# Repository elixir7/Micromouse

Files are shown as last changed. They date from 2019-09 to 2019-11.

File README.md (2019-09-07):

# Jerry the micromouse
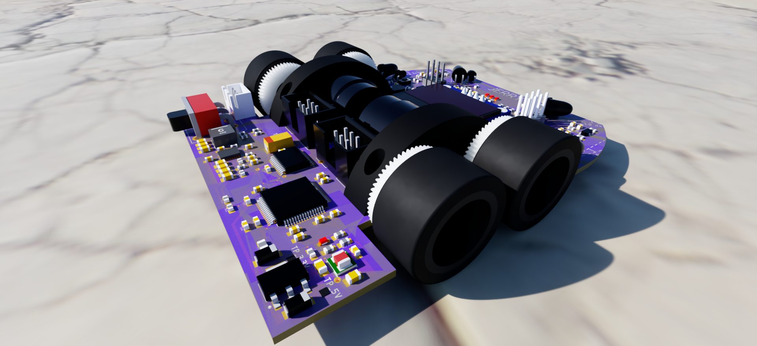
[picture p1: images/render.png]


# Who is Jerry?
Jerry is a tiny (10x8 cm) high performance robot for the robotics competition Micromouse. 

The competition goal is to search a 16x16 grid maze which is 3x3 m^2 as fast as possible and find the path to the center.

Then you run from start to goal with your calculated route. 

To get the competition you take 1/30 of the search time and the run time.

World class mice are extremly fast, [have a look.](https://www.youtube.com/watch?v=NqdZ9wbXt8k&t=150s)

# Structure & Development
Hardware:
-   <b>3D_Models</b>,       pcb components, motor mount, rims etc.
-   <b>drawings</b>,        .dxf files
-   <b>pcb</b>,             EAGLE CAD files
-   <b>gerbers.zip</b>,     manufacturing files for pcb (Jerry was made by [JLC PCB](https://www.jlcpcb.com)
-   <b>jlcpcb.cam</b>,      CAM job for creating gerber files to JLC standard in EAGLE.

Software:
-   <b>Eagle</b>,           E-CAD for making PCB
-   <b>Fusion 360</b>,      M-CAD for making board outline, motor mounts, rims, etc.
-   <b>Keil uVision 5</b>,  IDE for C programming/debugging on Microcontrollers

Images:
-   Renders of jerry

## Software
- MCU configuration (pins, clock, etc) using STM32CubeMX
- Keil uVision 5 project
    - Low level drivers (motors, sensors, screen)
    - High level maze solving algoritm

## Contributors
-   Isak Åslund, aslundisak@gmail.com

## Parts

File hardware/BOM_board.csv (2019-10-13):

Cart | # | Placed | Parts | Value | Package | Qty | Description | Device | TOLERANCE | V_RATING | Vendor | Link
x | 1 |  | BOOT |  | 2X03 | 1 | PIN HEADER | PINHD-2X3 |  |  | case/crf
x | 2 |  | DEBUG |  | 2X04 | 1 | PIN HEADER | PINHD-2X4 |  |  | case/crf
x | 3 |  | R32, R35, R36, R37 | 0 | R0603 | 4 | Standard Chip RESISTOR 0603 (1608 Metric) | R0603 |  |  | mouser
x | 4 |  | C1, C2, C4, C6, C8, C10, C12, C14, C18, C28, C30, C34, C35, C36, C43, C47, C48, C49, C50, C51 | 0.1u | C0603 | 20 | Standard Chip CAPACITOR 0605 (1608 Metric) | C0603 |  |  | mouser
x | 5 |  | C16 | 0.1u | C0805 | 1 | Standard Chip CAPACITOR 0805 (2012 Metric) | C0805 |  |  | mouser
x | 6 |  | R6, R7, R9, R12 | 0.75 | R0603 | 4 | Standard Chip RESISTOR 0603 (1608 Metric) | R0603 |  |  | mouser
x | 7 |  | R1, R2, R13, R16 | 1.8k | R0603 | 4 | Standard Chip RESISTOR 0603 (1608 Metric) | R0603 |  |  | mouser
x | 8 |  | R29 | 100k | R0603 | 1 | Standard Chip RESISTOR 0603 (1608 Metric) | R0603 |  |  | mouser
x | 9 |  | R_FBT | 105k | R0603 | 1 | Standard Chip RESISTOR 0603 (1608 Metric) | R0603 |  |  | mouser
x | 10 |  | R23 | 10k | R0603 | 1 | Standard Chip RESISTOR 0603 (1608 Metric) | R0603 | 1% |  | mouser
x | 11 |  | R3, R8, R10, R11, R15, R24, R27, R30, R31, R33, R34 | 10k | R0603 | 11 | Standard Chip RESISTOR 0603 (1608 Metric) | R0603 |  |  | mouser
x | 12 |  | C5, C7, C9, C11, C13, C42 | 10u | C0603 | 6 | Standard Chip CAPACITOR 0605 (1608 Metric) | C0603 |  |  | mouser
x | 13 |  | C_IN, C_OUT | 10u | C0805 | 2 | Standard Chip CAPACITOR 0805 (2012 Metric) | C0805 |  |  | mouser
x | 14 |  | C3 | 10u | EIA_6032-28 | 1 | KEMET C Size Taltalum Capacitator | KEMET_C |  |  | mouser
x | 15 |  | C26, C27 | 10u | SMC_A | 2 | A Size Taltalum Capacitator | SMC_A |  |  | mouser
x | 16 |  | FP1, FP2 | 10u | R0805 | 2 | Würth Electronics Size 0805 Ferrite Pearls | WE-CBF_0805 |  |  | mouser
x | 17 |  | R21 | 112k | R0603 | 1 | Standard Chip RESISTOR 0603 (1608 Metric) | R0603 |  |  | mouser
x | 18 |  | R17, RB | 150k | R0603 | 2 | Standard Chip RESISTOR 0603 (1608 Metric) | R0603 |  |  | mouser
x | 19 |  | R18 | 180k | R0603 | 1 | Standard Chip RESISTOR 0603 (1608 Metric) | R0603 |  |  | mouser
x | 20 |  | U$1 | 1N4148WX | 1N4148WX_SOD-323-2 | 1 |  | DIODE_1N4148WX |  |  | mouser
x | 21 |  | R4, R5, R14, R25 | 1k | R0603 | 4 | Standard Chip RESISTOR 0603 (1608 Metric) | R0603 |  |  | mouser
x | 22 |  | C44 | 1u | C0603 | 1 | Standard Chip CAPACITOR 0605 (1608 Metric) | C0603 |  |  | mouser
x | 23 |  | C24 | 1u | C0805 | 1 | Standard Chip CAPACITOR 0805 (2012 Metric) | C0805 |  |  | mouser
x | 24 |  | C15, C29, C45, C46 | 2.2u | C0603 | 4 | Standard Chip CAPACITOR 0605 (1608 Metric) | C0603 |  |  | mouser
x | 25 |  | L1 | 2.2u | XAL5030 | 1 | COILCRAFT - XAL5030-222MEC - INDUCTOR, PWR, 2.2UH, 9.2A,20%,38MHZ | XAL5030-222MEC |  |  | mouser
x | 26 |  | R19, R26, R28, R_FBB | 20k | R0603 | 4 | Standard Chip RESISTOR 0603 (1608 Metric) | R0603 |  |  | mouser
x | 27 |  | C17, C19, C20, C22, C25 | 22u | C0805 | 5 | Standard Chip CAPACITOR 0805 (2012 Metric) | C0805 |  |  | mouser
x | 28 |  | C33 | 22u | C0805 | 1 | Standard Chip CAPACITOR 0805 (2012 Metric) | C0805 |  | 10v | mouser
x | 29 |  | C32 | 22u | C0805 | 1 | Standard Chip CAPACITOR 0805 (2012 Metric) | C0805 |  | 25V | mouser
x | 30 |  | C21 | 27p | C0603 | 1 | Standard Chip CAPACITOR 0605 (1608 Metric) | C0603 |  |  | mouser
x | 31 |  | RT | 290k | R0603 | 1 | Standard Chip RESISTOR 0603 (1608 Metric) | R0603 | 1% |  | mouser
x | 32 |  | R20 | 30k | R0603 | 1 | Standard Chip RESISTOR 0603 (1608 Metric) | R0603 |  |  | mouser
x | 33 |  | C31 | 3300p | C0603 | 1 | Standard Chip CAPACITOR 0605 (1608 Metric) | C0603 |  | 10V | mouser
x | 34 |  | C_VC | 470pF | C0603 | 1 | Standard Chip CAPACITOR 0605 (1608 Metric) | C0603 |  | 6.3V | mouser
x | 35 |  | R22 | 47k | R0603 | 1 | Standard Chip RESISTOR 0603 (1608 Metric) | R0603 |  |  | mouser
x | 36 |  | C23 | 560p | C0603 | 1 | Standard Chip CAPACITOR 0605 (1608 Metric) | C0603 |  |  | mouser
x | 37 |  | U4 | BMI088 | PQFN50P450X300X100-16N | 1 | High-performance 6-axis inertial sensor (accelerometer + gyroscope) | BMI088 |  |  | mouser
x | 38 |  | 5V_PWR, LED_B, LED_G, LED_R | CHIP-LED0603 | CHIP-LED0603 | 4 | CHIP-LED0603 (SMD) | CHIP-LED0603 |  |  | mouser
x | 39 |  | OLED | DISPLAY-OLED-128X64-I2C | DISPLAY-OLED-128X64-I2C | 1 | 128x64 Dot Matrix OLED Module based on SSD1306 chip | DISPLAY-OLED-128X64-I2C |  |  | mouser
x | 40 |  | MOTOR_LEFT, MOTOR_RIGHT | IE2-1024-ENCODER | IE2-1024-ENCODER | 2 |  | IE2-1024-ENCODER |  |  | mouser
x | 41 |  | Q1, Q2, Q3, Q4, Q5 | IRFML8244TRPBF | SOT95P235X110-3 | 5 | IRFML8244TRPbF - N Channel Mosfet | IRFML8244TRPBF |  |  | mouser
x | 42 |  | U$10 | JST-XH-3 | JST-XH-03 | 1 |  | JST-XH-3 |  |  | mouser
x | 43 |  | BTN_RST, BTN_SEL | KMR621NGLFS | KMR621NGLFS | 2 | C&K KMR621NG LFS Tactile SPST switch (SMD) | KMR621NGLFS |  |  | mouser
x | 44 |  | VR1 | LM1117-3.3 | SOT230P700X180-4 | 1 | LM1117 | LM1117-3.3 |  |  | mouser
x | 45 |  | IC3 | LMZ10501 | SON65P260X300X150-9N | 1 | Voltage Regulators - Switching Regulators 1A Nano Mod w/ 5.5V Max Inpt VTG | LMZ10501 |  |  | mouser
x | 46 |  | S1 | LMZ21701 | LMZ21701 | 1 | 3V to 17V, 1A Step-Down DC/DC Power Module in 3.5mm 3.5mm Package | LMZ21701 |  |  | mouser
x | 47 |  | FL_EMITTER, FR_EMITTER, L_EMITTER, R_EMITTER | SFH_4545 | SFH_4545 | 4 | High Power Infrared Emitter (940 nm) | SFH_4545 |  |  | mouser
x | 48 |  | U$4 | SMT-0540-S-R | SMT-0540-S-R | 1 | Magnetic buzzer | SMT-0540-S-R |  |  | mouser
x | 49 |  | SW | SPDT-500SSP1S1M6QEA | 500SSP1S1M6QEA | 1 |  | SPDT-500SSP1S1M6QEA |  |  | mouser
NA | 50 |  | U$6, U$7 | SPLITTER | SPLITTER | 2 | Used for separating grounds | SPLITTER |  |  | NA
x | 51 |  | U3 | STM32F405RG | LQFP-64 | 1 | STM32F405RG Microcontroller | STM32F405RG |  |  | mouser
x | 52 |  | U1 | TB6612FNG | SOP65P760X160-24 | 1 | TB6612FNG - Dual DC motor driver | TB6612FNG |  |  | mouser
x | 53 |  | D4, D5, D6, D8 | TEFT4300 | 3MM_PHOTOTRANSISTOR | 4 | TEFT4300 Phototransistor from Vishay | TEFT4300 |  |  | mouser
NA | 54 |  | TP_2V, TP_3.3V, TP_5V, TP_12V | TEST-POINT3X5 | PAD.03X.05 | 4 | SparkFun Test Points | TEST-POINT3X5 |  |  | NA
x | 55 |  | IC2 | TPS61088RHLR | RHL(R-PVQFN-N20)_1 | 1 | DC-DC Boost Regulator | TPS61088RHLR |  |  | mouser
x | 56 |  | HC-05 | WIRELESS-BLUETOOTH-HC-05 | WIRELESS-BLUETOOTH-HC-05 | 1 | Bluetooth Transceiver Module based on HC-05 board | WIRELESS-BLUETOOTH-HC-05 |  |  | mouser

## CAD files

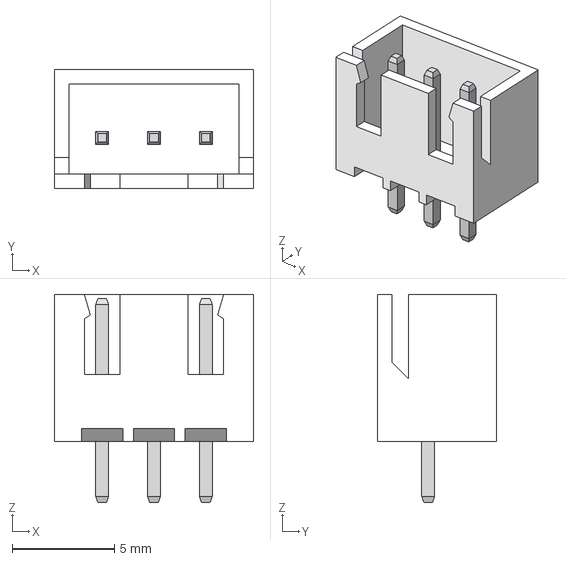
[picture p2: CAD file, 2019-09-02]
hardware/3D_Models/JST-XH-03.step
9.75 x 5.84 x 10.2 mm

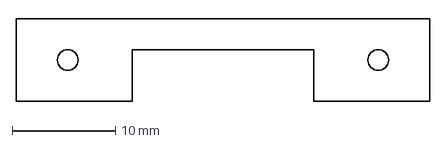
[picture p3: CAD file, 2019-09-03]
hardware/drawings_dxf/motor_mount.dxf
40.0 x 8.00 mm

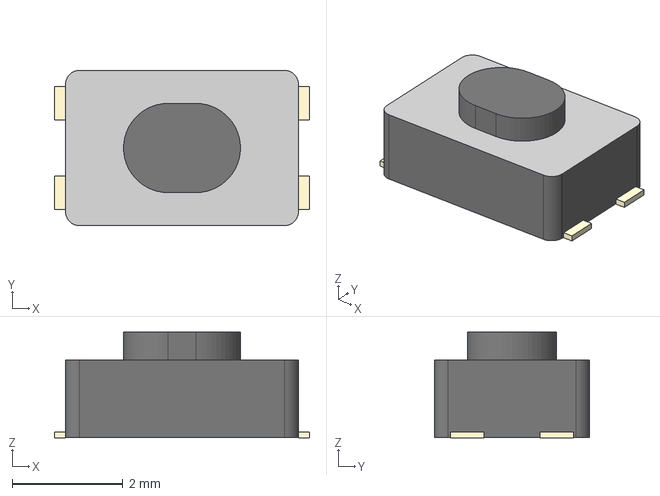
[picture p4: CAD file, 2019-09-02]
hardware/3D_Models/KMR621NGLFS.step
4.60 x 2.80 x 1.91 mm

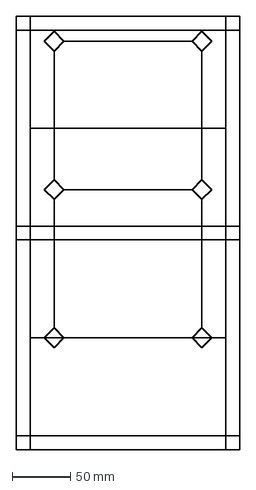
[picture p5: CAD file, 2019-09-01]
hardware/drawings_dxf/maze_dimenions.dxf
192.0 x 372.0 mm

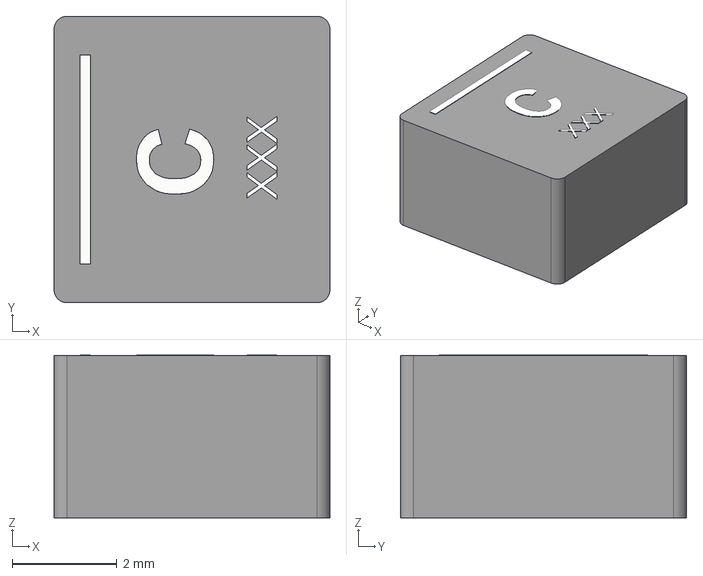
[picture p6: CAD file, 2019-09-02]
hardware/3D_Models/HALX5030-222.step
5.28 x 5.48 x 3.11 mm

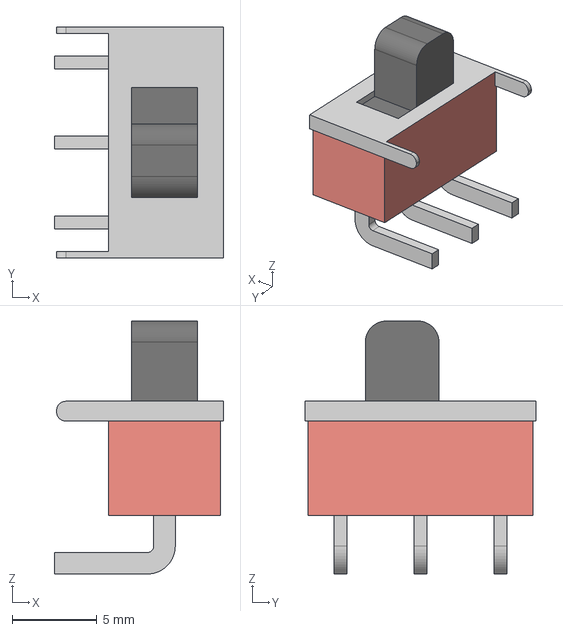
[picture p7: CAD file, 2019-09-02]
hardware/3D_Models/500SSP1S1M6QEA-Switch.step
9.96 x 13.6 x 14.9 mm

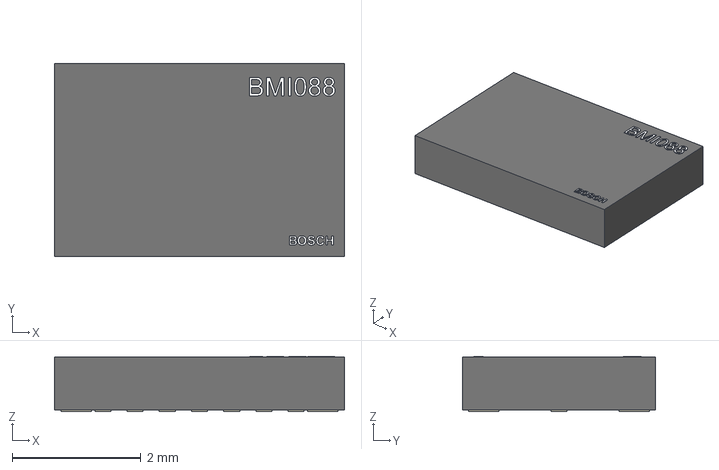
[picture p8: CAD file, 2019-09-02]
hardware/3D_Models/BMI088.step
4.50 x 3.00 x 0.86 mm

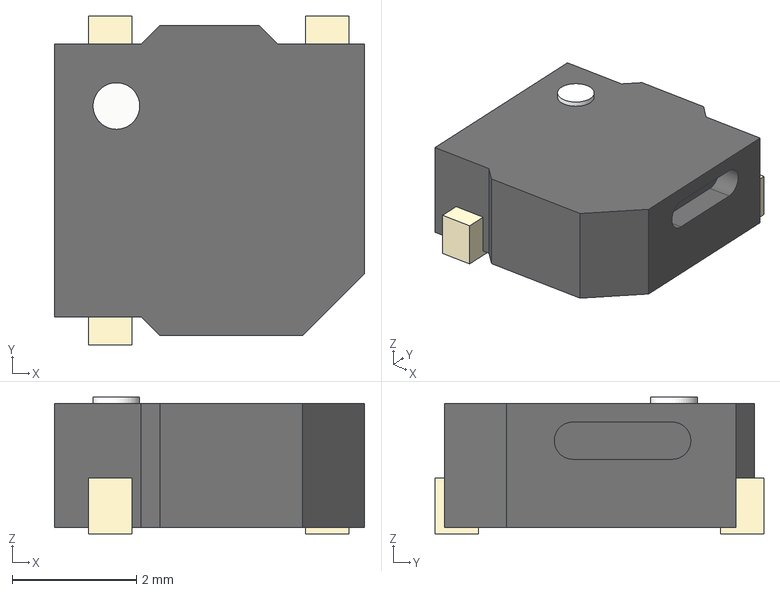
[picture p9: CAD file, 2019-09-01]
hardware/3D_Models/SMT-0540-SR.step
5.00 x 5.30 x 2.20 mm

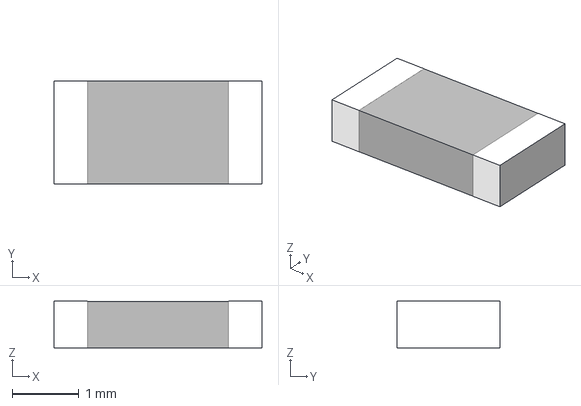
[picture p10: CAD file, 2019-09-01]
hardware/3D_Models/R1206.step
3.12 x 1.55 x 0.7 mm

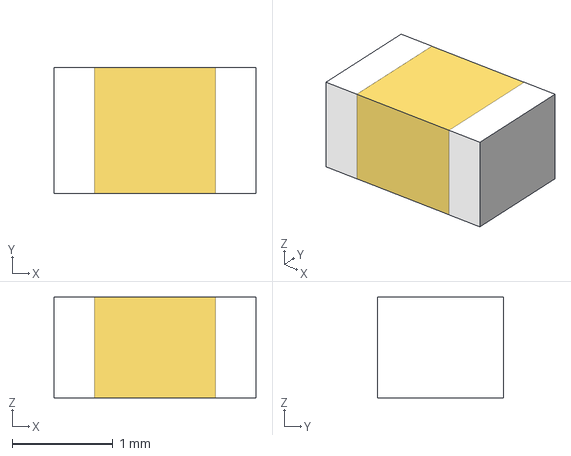
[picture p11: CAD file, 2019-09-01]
hardware/3D_Models/C0805.step
2.00 x 1.25 x 1.00 mm

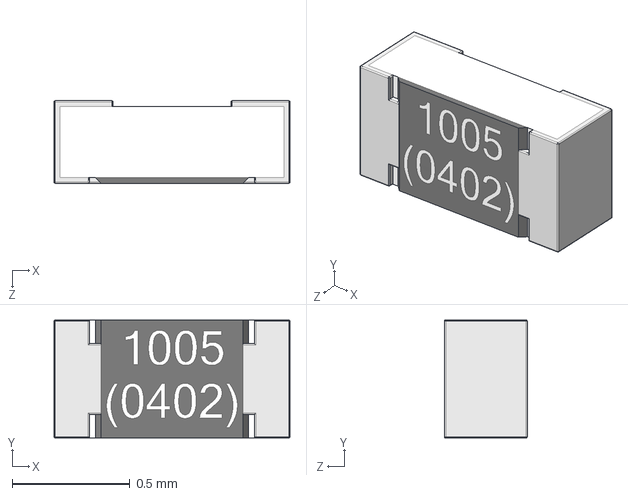
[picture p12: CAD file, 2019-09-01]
hardware/3D_Models/R0402.step
1.00 x 0.5 x 0.35 mm

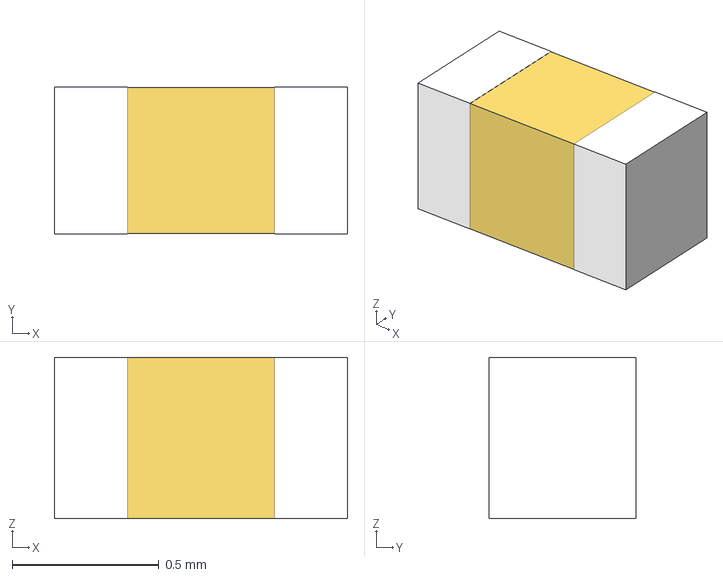
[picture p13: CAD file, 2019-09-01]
hardware/3D_Models/C0402.step
1.00 x 0.5 x 0.55 mm

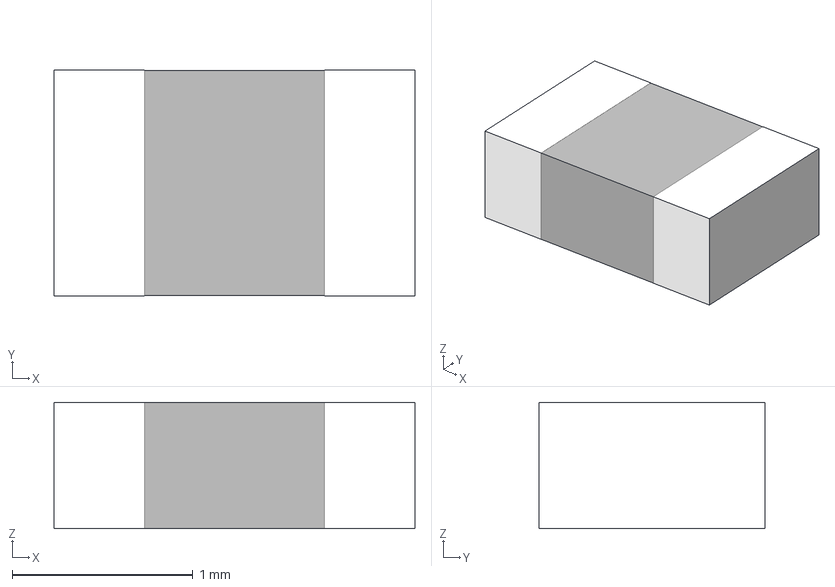
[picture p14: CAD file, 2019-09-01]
hardware/3D_Models/R0805.step
2.00 x 1.25 x 0.7 mm

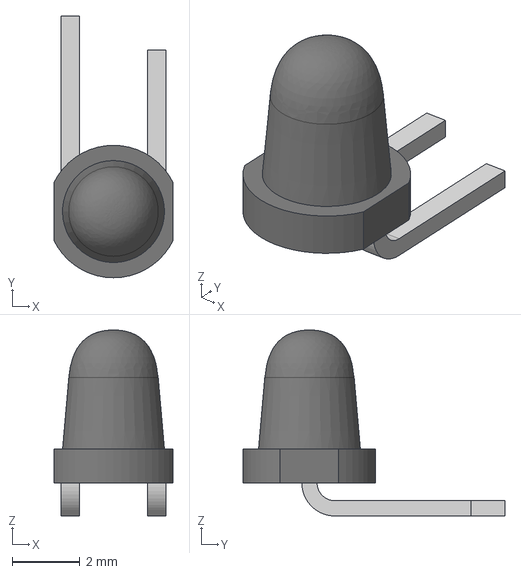
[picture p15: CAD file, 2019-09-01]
hardware/3D_Models/TEFT4300.step
3.50 x 7.70 x 5.47 mm

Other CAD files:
hardware/3D_Models/C1206.step
hardware/3D_Models/IDC-6.step
hardware/3D_Models/MicroSIP_8.step
hardware/3D_Models/HC-05.step
hardware/3D_Models/C0603.step
hardware/3D_Models/Faulhaber_1717SR006.f3z
hardware/3D_Models/OLED_0.96_64x128.step
hardware/3D_Models/R0603.step
hardware/3D_Models/SFH4545.step
hardware/3D_Models/tps61088.step
hardware/3D_Models/uSip_8.step

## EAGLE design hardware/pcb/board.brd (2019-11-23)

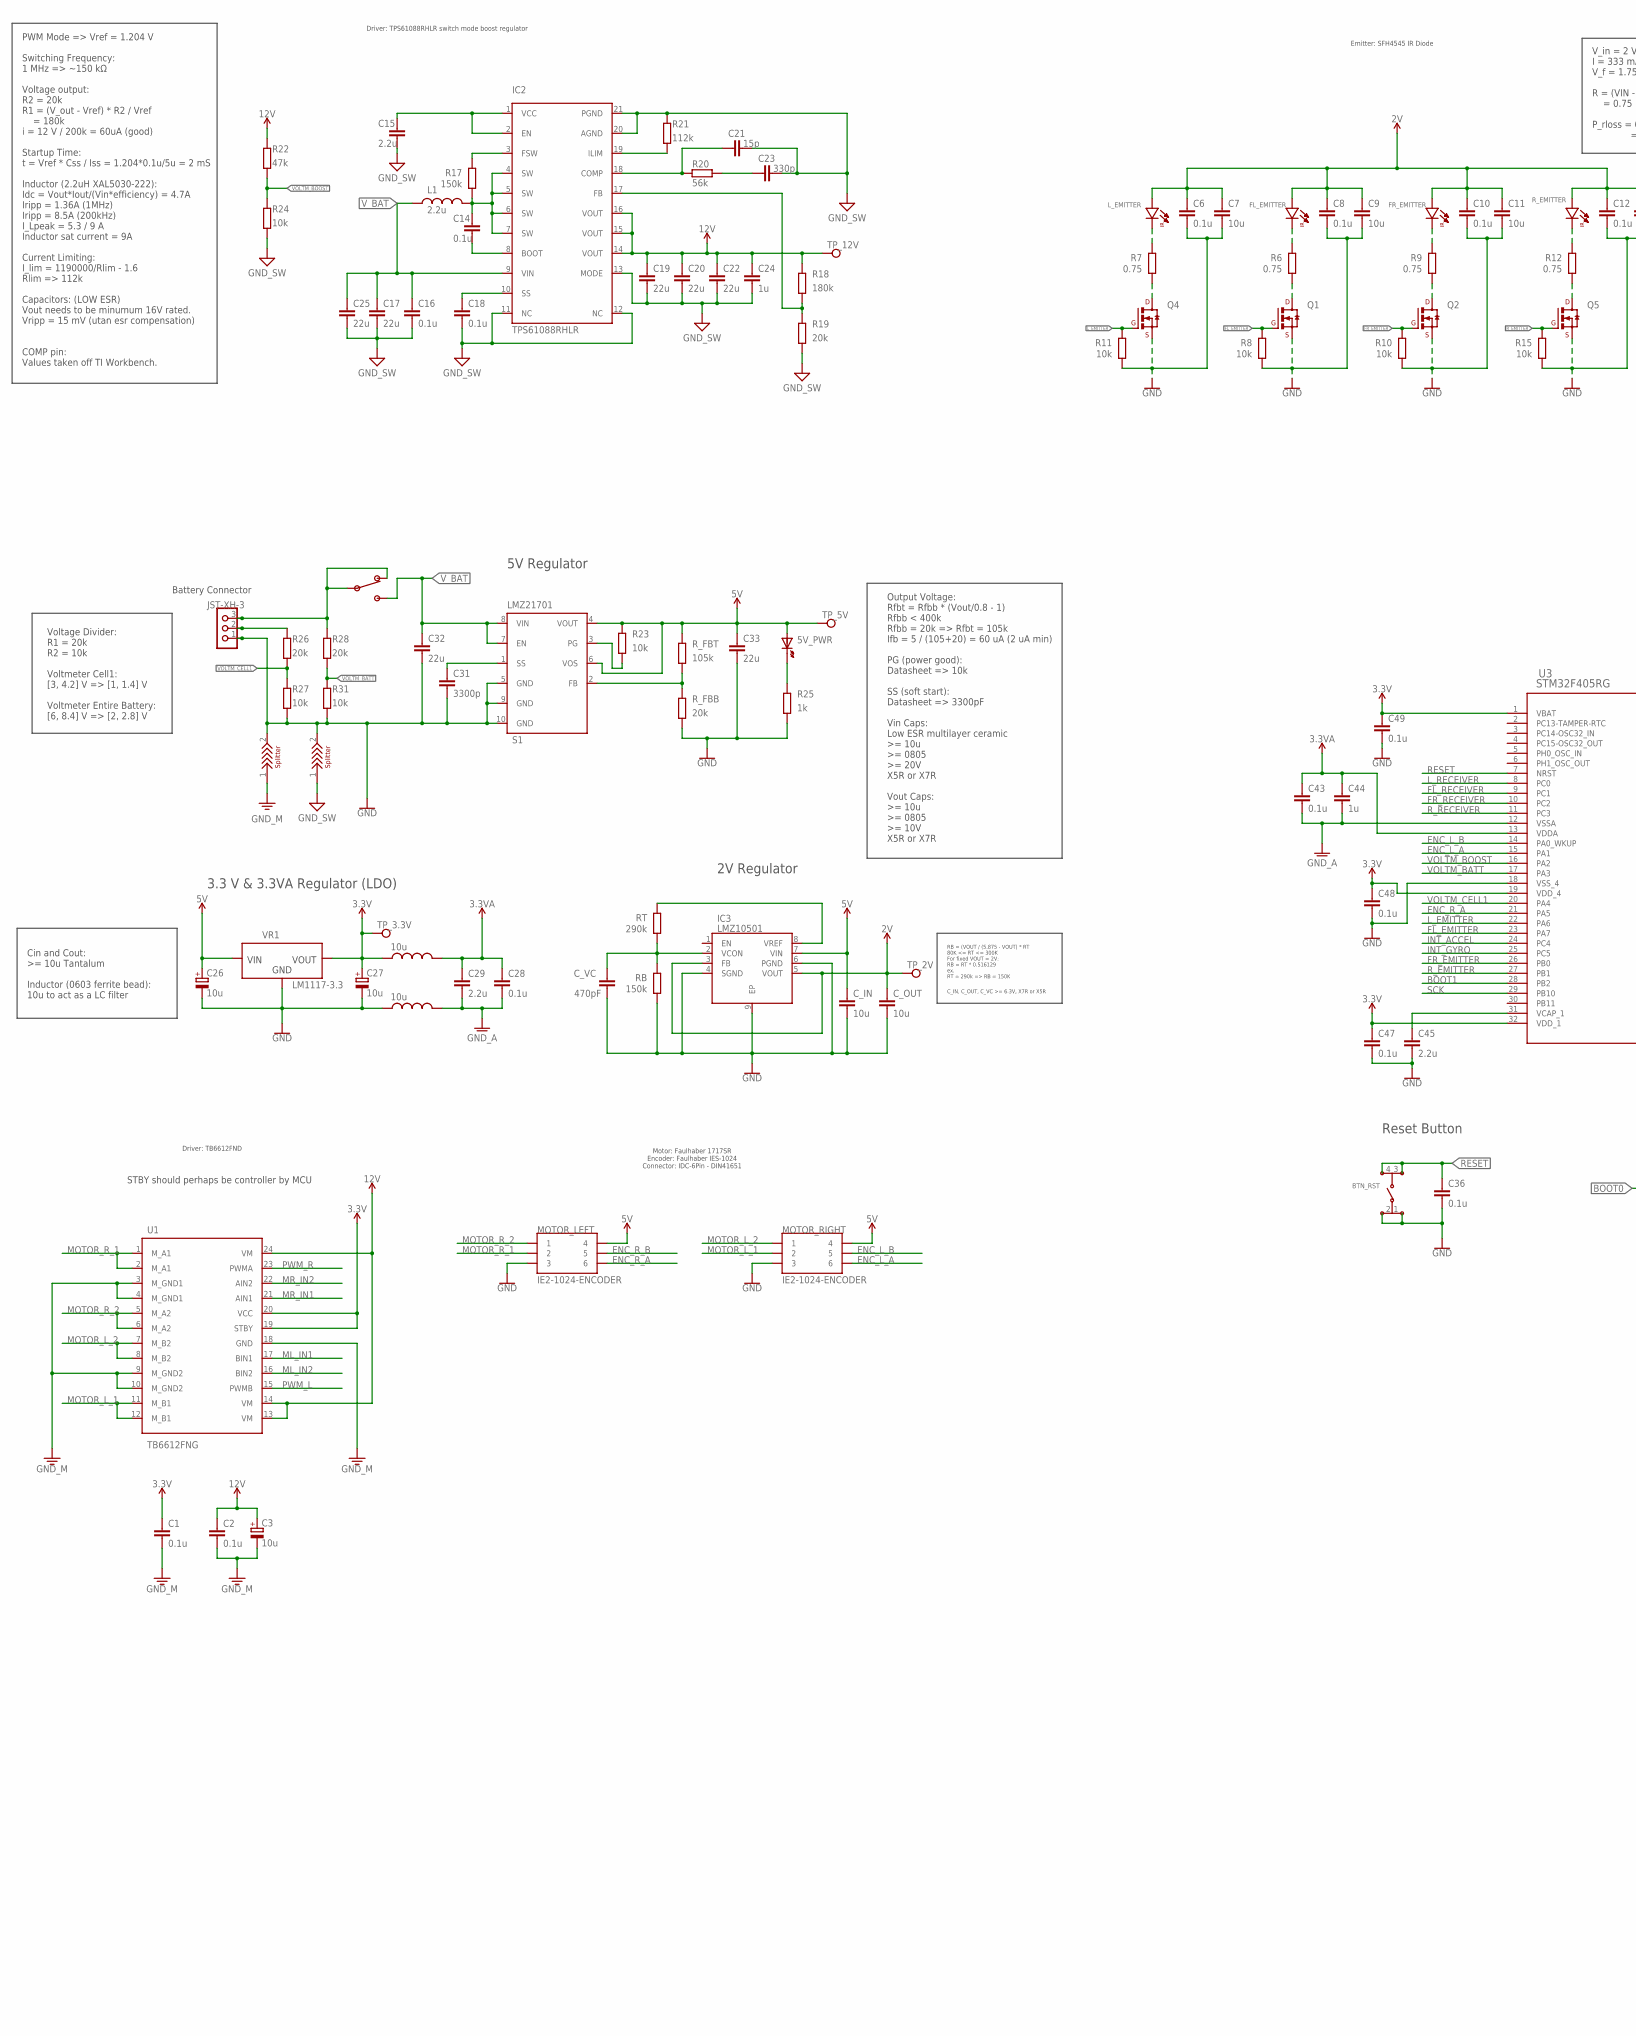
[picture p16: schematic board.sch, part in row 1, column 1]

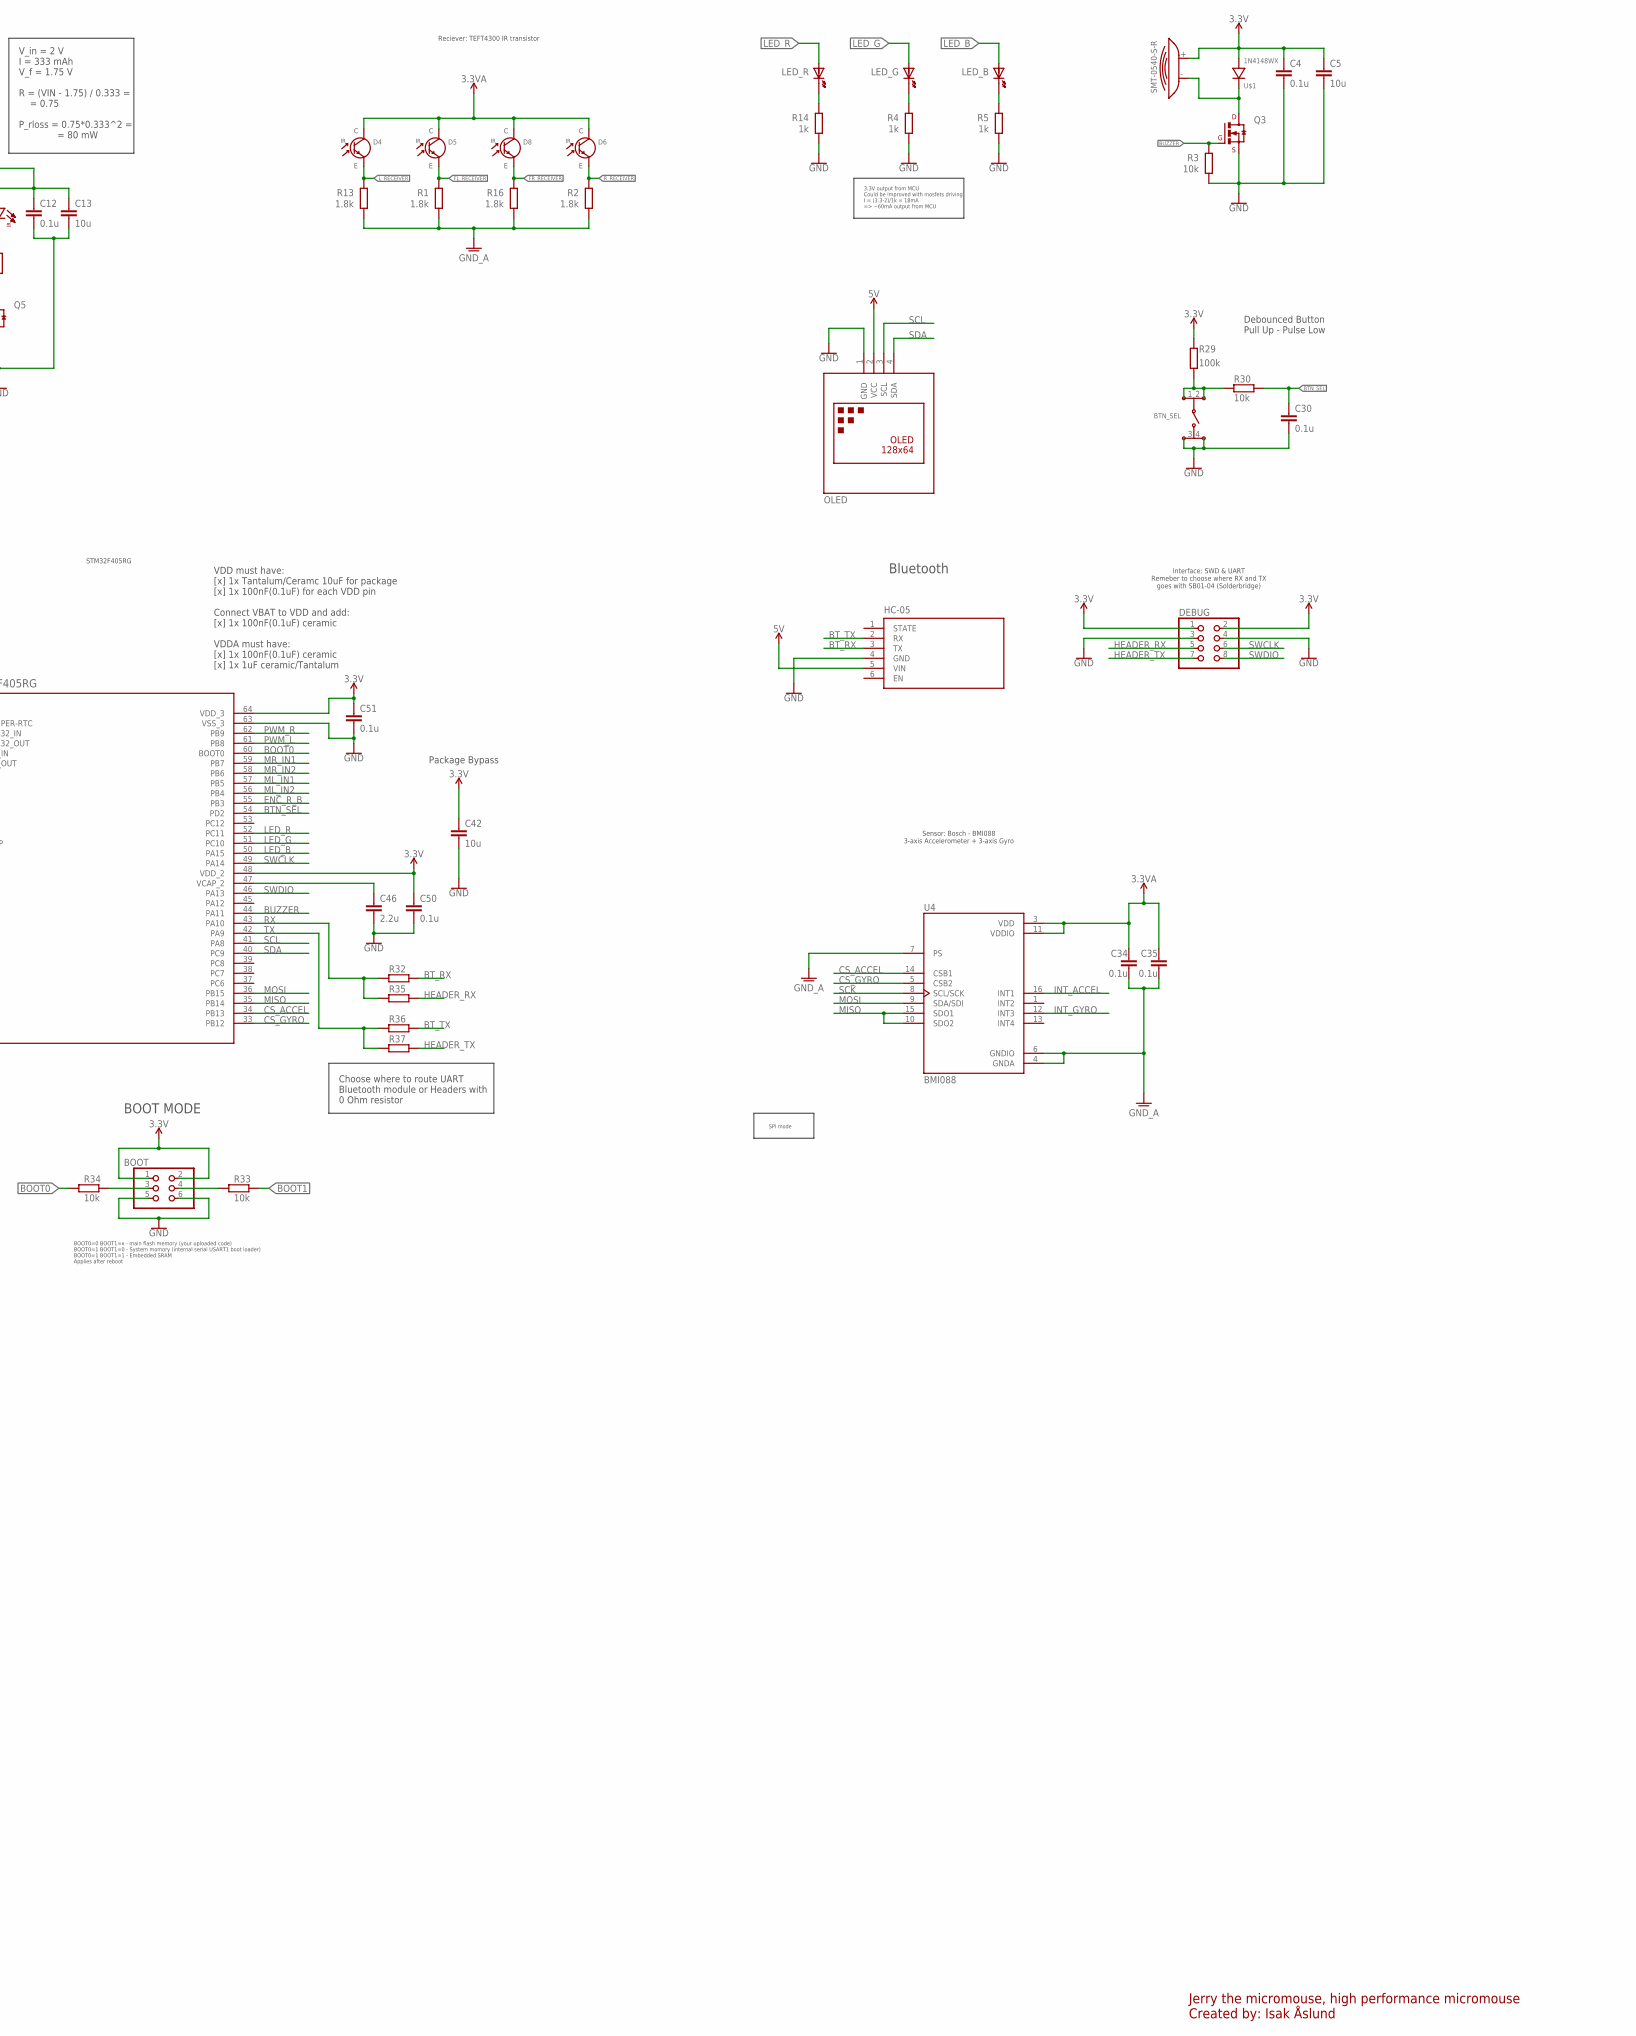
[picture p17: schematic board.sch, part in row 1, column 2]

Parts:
5V_PWR: CHIP-LED0603
BOOT: PINHD-2X3; 2X03
BTN_RST: KMR621NGLFS
BTN_SEL: KMR621NGLFS
C1, C2, C4, C6, C8, C10, C12, C14, C18, C28, C30, C34, C35, C36, C43, C47, C48, C49, C50, C51: 0.1u; C0603
C3: 10u; EIA_6032-28
C5, C7, C9, C11, C13, C42: 10u; C0603
C15, C29, C45, C46: 2.2u; C0603
C16: 0.1u; C0805
C17, C19, C20, C22, C25, C33: 22u; C0805
C21: 15p; C0603
C23: 330p; C0603
C24: 1u; C0805
C26, C27: 10u; SMC_A
C31: 3300p; C0603; RATING X5R/X7R
C32: 22u; C0805; RATING X5R/X7R
C44: 1u; C0603
C_IN: 10u; C0805
C_OUT: 10u; C0805
C_VC: 470pF; C0603; RATING X5R/X7R
D4, D5, D6, D8: TEFT4300; 3MM_PHOTOTRANSISTOR
DEBUG: PINHD-2X4; 2X04
FL_EMITTER: SFH_4545
FP1, FP2: 10u; R0805
FR_EMITTER: SFH_4545
HC-05: WIRELESS-BLUETOOTH-HC-05
IC2: TPS61088RHLR; RHL(R-PVQFN-N20)_1
IC3: LMZ10501; SON65P260X300X150-9N
L1: 2.2u; XAL5030
LED_B: CHIP-LED0603
LED_G: CHIP-LED0603
LED_R: CHIP-LED0603
L_EMITTER: SFH_4545
MOTOR_LEFT: IE2-1024-ENCODER
MOTOR_RIGHT: IE2-1024-ENCODER
OLED: DISPLAY-OLED-128X64-I2C
Q1, Q2, Q3, Q4, Q5: IRFML8244TRPBF; SOT95P235X110-3
R1, R2, R13, R16: 1.8k; R0603
R3, R8, R10, R11, R15, R24, R27, R30, R31, R33, R34: 10k; R0603
R4, R5, R14, R25: 1k; R0603
R6, R7, R9, R12: 0.75; R0603
R17: 150k; R0603
R18: 180k; R0603
R19, R26, R28: 20k; R0603
R20: 56k; R0603
R21: 112k; R0603
R22: 47k; R0603
R23: 10k; R0603; TOLERANCE 1%
R29: 100k; R0603
R32, R35, R36, R37: 0; R0603
RB: 150k; R0603
RT: 290k; R0603; TOLERANCE 1%
R_EMITTER: SFH_4545
R_FBB: 20k; R0603
R_FBT: 105k; R0603
S1: LMZ21701
SW: SPDT-500SSP1S1M6QEA; 500SSP1S1M6QEA
TP_2V, TP_3.3V, TP_5V, TP_12V: TEST-POINT3X5; PAD.03X.05
U1: TB6612FNG; SOP65P760X160-24
U3: STM32F405RG; LQFP-64
U4: BMI088; PQFN50P450X300X100-16N
U$1: 1N4148WX; 1N4148WX_SOD-323-2
U$4: SMT-0540-S-R
U$6, U$7: SPLITTER
U$10: JST-XH-3; JST-XH-03
VR1: LM1117-3.3; SOT230P700X180-4

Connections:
2V: C6.1, C7.1, C8.1, C9.1, C10.1, C11.1, C12.1, C13.1, C_OUT.1, FL_EMITTER.+ (+_ANODE), FR_EMITTER.+ (+_ANODE), IC3.3 (FB), IC3.5 (VOUT), L_EMITTER.+ (+_ANODE), R_EMITTER.+ (+_ANODE), TP_2V.P$1
3.3V: BOOT.1, BOOT.2, C1.1, C4.1, C5.1, C27.+, C42.1, C47.1, C48.1, C49.1, C50.1, C51.1, DEBUG.1, DEBUG.2, FP1.1, R29.1, TP_3.3V.P$1, U1.19 (STBY), U1.20 (VCC), U3.1 (VBAT), U3.19 (VDD_4), U3.32 (VDD_1), U3.48 (VDD_2), U3.64 (VDD_3), U$1.+ (+_ANODE), U$4.+, VR1.2 (VOUT), VR1.4 (VOUT)
3.3VA: C28.1, C29.1, C34.1, C35.1, C43.1, C44.1, D4.C (C_+), D5.C (C_+), D6.C (C_+), D8.C (C_+), FP1.2, U3.13 (VDDA), U4.3 (VDD), U4.11 (VDDIO)
5V: 5V_PWR.A, C26.+, C33.1, C_IN.1, HC-05.5 (VIN), IC3.7 (VIN), MOTOR_LEFT.4, MOTOR_RIGHT.4, OLED.2 (VCC), R23.2, R_FBT.1, S1.4 (VOUT), S1.6 (VOS), TP_5V.P$1, VR1.3 (VIN)
12V: C2.1, C3.1 (+), C19.1, C20.1, C22.1, C24.1, IC2.14 (VOUT), IC2.15 (VOUT), IC2.16 (VOUT), R18.1, R22.2, TP_12V.P$1, U1.13 (VM), U1.14 (VM), U1.24 (VM)
BOOT0: R34.2, U3.60 (BOOT0)
BOOT1: R33.1, U3.28 (PB2)
BTN_SEL: C30.1, R30.2, U3.54 (PD2)
BT_RX: HC-05.3 (TX), R32.2
BT_TX: HC-05.2 (RX), R36.2
BUZZER: Q3.1 (G), R3.2, U3.44 (PA11)
CS_ACCEL: U3.34 (PB13), U4.14 (CSB1)
CS_GYRO: U3.33 (PB12), U4.5 (CSB2)
ENC_L_A: MOTOR_RIGHT.6, U3.15 (PA1)
ENC_L_B: MOTOR_RIGHT.5, U3.14 (PA0_WKUP)
ENC_R_A: MOTOR_LEFT.6, U3.21 (PA5)
ENC_R_B: MOTOR_LEFT.5, U3.55 (PB3)
FL_EMITTER: Q1.1 (G), R8.2, U3.23 (PA7)
FL_RECEIVER: D5.E (E_-), R1.2, U3.9 (PC1)
FR_EMITTER: Q2.1 (G), R10.2, U3.26 (PB0)
FR_RECEIVER: D8.E (E_-), R16.2, U3.10 (PC2)
GND: BOOT.5, BOOT.6, BTN_RST.1, BTN_RST.2, BTN_SEL.3, BTN_SEL.4, C4.2, C5.2, C6.2, C7.2, C8.2, C9.2, C10.2, C11.2, C12.2, C13.2, C26.-, C27.-, C30.2, C31.2, C32.2, C33.2, C36.2, C42.2, C45.2, C46.2, C47.2, C48.2, C49.2, C50.2, C51.2, C_IN.2, C_OUT.2, C_VC.2, DEBUG.3, DEBUG.4, FP2.1, HC-05.4 (GND), IC3.4 (SGND), IC3.6 (PGND), IC3.9 (EP), MOTOR_LEFT.3, MOTOR_RIGHT.3, OLED.1 (GND), Q1.2 (S), Q2.2 (S), Q3.2 (S), Q4.2 (S), Q5.2 (S), R3.1, R4.1, R5.1, R8.1, R10.1, R11.1, R14.1, R15.1, R25.1, R27.1, R31.1, RB.1, R_FBB.1, S1.5 (GND), S1.9 (GND), S1.10 (GND), U3.18 (VSS_4), U3.63 (VSS_3), U$6.2, U$7.2, U$10.1, VR1.1 (GND)
GND_A: C28.2, C29.2, C34.2, C35.2, C43.2, C44.2, FP2.2, R1.1, R2.1, R13.1, R16.1, U3.12 (VSSA), U4.4 (GNDA), U4.6 (GNDIO), U4.7 (PS)
GND_M: C1.2, C2.2, C3.2 (-), U1.3 (M_GND1), U1.4 (M_GND1), U1.9 (M_GND2), U1.10 (M_GND2), U1.18 (GND), U$6.1
GND_SW: C15.2, C16.2, C17.2, C18.2, C19.2, C20.2, C21.2, C22.2, C23.2, C24.2, C25.2, IC2.11 (NC), IC2.12 (NC), IC2.13 (MODE), IC2.20 (AGND), IC2.21 (PGND), R19.2, R21.2, R24.1, U$7.1
HEADER_RX: DEBUG.5, R35.2
HEADER_TX: DEBUG.7, R37.2
INT_ACCEL: U3.24 (PC4), U4.16 (INT1)
INT_GYRO: U3.25 (PC5), U4.12 (INT3)
LED_B: LED_B.A, U3.50 (PA15)
LED_G: LED_G.A, U3.51 (PC10)
LED_R: LED_R.A, U3.52 (PC11)
L_EMITTER: Q4.1 (G), R11.2, U3.22 (PA6)
L_RECEIVER: D4.E (E_-), R13.2, U3.8 (PC0)
MISO: U3.35 (PB14), U4.10 (SDO2), U4.15 (SDO1)
ML_IN1: U1.17 (BIN1), U3.57 (PB5)
ML_IN2: U1.16 (BIN2), U3.56 (PB4)
MOSI: U3.36 (PB15), U4.9 (SDA/SDI)
MOTOR_L_1: MOTOR_RIGHT.2, U1.11 (M_B1), U1.12 (M_B1)
MOTOR_L_2: MOTOR_RIGHT.1, U1.7 (M_B2), U1.8 (M_B2)
MOTOR_R_1: MOTOR_LEFT.2, U1.1 (M_A1), U1.2 (M_A1)
MOTOR_R_2: MOTOR_LEFT.1, U1.5 (M_A2), U1.6 (M_A2)
MR_IN1: U1.21 (AIN1), U3.59 (PB7)
MR_IN2: U1.22 (AIN2), U3.58 (PB6)
unnamed: Q4.3 (D), R7.1
unnamed: L_EMITTER.- (-_CATHODE), R7.2
unnamed: LED_R.C (K), R14.2
unnamed: Q1.3 (D), R6.1
unnamed: FL_EMITTER.- (-_CATHODE), R6.2
unnamed: LED_G.C (K), R4.2
unnamed: Q5.3 (D), R12.1
unnamed: Q2.3 (D), R9.1
unnamed: LED_B.C (K), R5.2
unnamed: IC3.8 (VREF), RT.2
unnamed: C_VC.1, IC3.2 (VCON), RB.2, RT.1
unnamed: R12.2, R_EMITTER.- (-_CATHODE)
unnamed: Q3.3 (D), U$1.- (-_CATHODE), U$4.-
unnamed: FR_EMITTER.- (-_CATHODE), R9.2
unnamed: C14.1, IC2.4 (SW), IC2.5 (SW), IC2.6 (SW), IC2.7 (SW), L1.2, R17.1
unnamed: IC2.3 (FSW), R17.2
unnamed: C14.2, IC2.8 (BOOT)
unnamed: C15.1, IC2.1 (VCC), IC2.2 (EN)
unnamed: C18.1, IC2.10 (SS)
unnamed: IC2.17 (FB), R18.2, R19.1
unnamed: C21.1, IC2.18 (COMP), R20.1
unnamed: IC2.19 (ILIM), R21.1
unnamed: C23.1, R20.2
unnamed: C31.1, S1.1 (SS)
unnamed: R_FBB.2, R_FBT.2, S1.2 (FB)
unnamed: R23.1, S1.3 (PG)
unnamed: 5V_PWR.C (K), R25.2
unnamed: BOOT.4, R33.2
unnamed: R26.2, U$10.2
unnamed: BOOT.3, R34.1
unnamed: BTN_SEL.1, BTN_SEL.2, R29.2, R30.1
unnamed: C45.1, U3.31 (VCAP_1)
unnamed: C46.1, U3.47 (VCAP_2)
unnamed: R28.2, SW.1, SW.2_COM (COM), U$10.3
PWM_L: U1.15 (PWMB), U3.61 (PB8)
PWM_R: U1.23 (PWMA), U3.62 (PB9)
RESET: BTN_RST.3, BTN_RST.4, C36.1, U3.7 (NRST)
RX: R32.1, R35.1, U3.43 (PA10)
R_EMITTER: Q5.1 (G), R15.2, U3.27 (PB1)
R_RECEIVER: D6.E (E_-), R2.2, U3.11 (PC3)
SCK: U3.29 (PB10), U4.8 (SCL/SCK)
SCL: OLED.3 (SCL), U3.41 (PA8)
SDA: OLED.4 (SDA), U3.40 (PC9)
SWCLK: DEBUG.6, U3.49 (PA14)
SWDIO: DEBUG.8, U3.46 (PA13)
TX: R36.1, R37.1, U3.42 (PA9)
VOLTM_BATT: R28.1, R31.2, U3.17 (PA3)
VOLTM_BOOST: R22.1, R24.2, U3.16 (PA2)
VOLTM_CELL1: R26.1, R27.2, U3.20 (PA4)
V_BAT: C16.1, C17.1, C25.1, C32.1, IC2.9 (VIN), L1.1, S1.7 (EN), S1.8 (VIN), SW.3

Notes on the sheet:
Reciever: TEFT4300 IR transistor
Emitter: SFH4545 IR Diode
Driver: TB6612FND
STM32F405RG
3.3V output from MCU Could be improved with mosfets driving I = (3.3-2)/1k = 18mA => ~60mA output from MCU
STBY should perhaps be controller by MCU
V_in = 2 V I = 333 mAh V_f = 1.75 V R = (VIN - 1.75) / 0.333 = = 0.75 P_rloss = 0.75*0.333^2 = = 80 mW
RB = (VOUT / (5.875 - VOUT) * RT 80K <= RT <= 300K For fixed VOUT = 2V: RB = RT * 0.516129 ex. RT = 290k => RB = 150K
C_IN, C_OUT, C_VC >= 6.3V, X7R or X5R
2V Regulator
PWM Mode => Vref = 1.204 V Switching Frequency: 1 MHz => ~150 kΩ Voltage output: R2 = 20k R1 = (V_out - Vref) * R2 / Vref = 180k i = 12 V / 200k = 60uA (good) Startup Time: t = Vref * Css / Iss = 1.204*0.1u/5u = 2 mS Inductor (2.2uH XAL5030-222): Idc = Vout*Iout/(Vin*efficiency) = 4.7A Iripp = 1.36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
5V Regulator
Output Voltage: Rfbt = Rfbb * (Vout/0.8 - 1) Rfbb < 400k Rfbb = 20k => Rfbt = 105k Ifb = 5 / (105+20) = 60 uA (2 uA min) PG (power good): Datasheet => 10k SS (soft start): Datasheet => 3300pF Vin Caps: Low ESR multilayer ceramic >= 10u >= 0805 >= 20V X5R or X7R Vout Caps: >= 10u >= 0805 >= 10V X5R 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
3.3 V & 3.3VA Regulator (LDO)
Cin and Cout: >= 10u Tantalum Inductor (0603 ferrite bead): 10u to act as a LC filter
Sensor: Bosch - BMI088 3-axis Accelerometer + 3-axis Gyro
Battery Connector
Voltage Divider: R1 = 20k R2 = 10k Voltmeter Cell1: [3, 4.2] V => [1, 1.4] V Voltmeter Entire Battery: [6, 8.4] V => [2, 2.8] V
SPI mode
Interface: SWD & UART Remeber to choose where RX and TX goes with SB01-04 (Solderbridge)
Motor: Faulhaber 1717SR Encoder: Faulhaber IES-1024 Connector: IDC-6Pin - DIN41651
Debounced Button Pull Up - Pulse Low
Reset Button
VDD must have: [x] 1x Tantalum/Ceramc 10uF for package [x] 1x 100nF(0.1uF) for each VDD pin Connect VBAT to VDD and add: [x] 1x 100nF(0.1uF) ceramic VDDA must have: [x] 1x 100nF(0.1uF) ceramic [x] 1x 1uF ceramic/Tantalum
Package Bypass
BOOT MODE
BOOT0=0 BOOT1=x - main flash memory (your uploaded code) BOOT0=1 BOOT1=0 - System momory (internal serial USART1 boot loader) BOOT0=1 BOOT1=1 - Embedded SRAM Applies after reboot
Bluetooth
Choose where to route UART Bluetooth module or Headers with 0 Ohm resistor
Driver: TPS61088RHLR switch mode boost regulator
Jerry the micromouse, high performance micromouse Created by: Isak Åslund

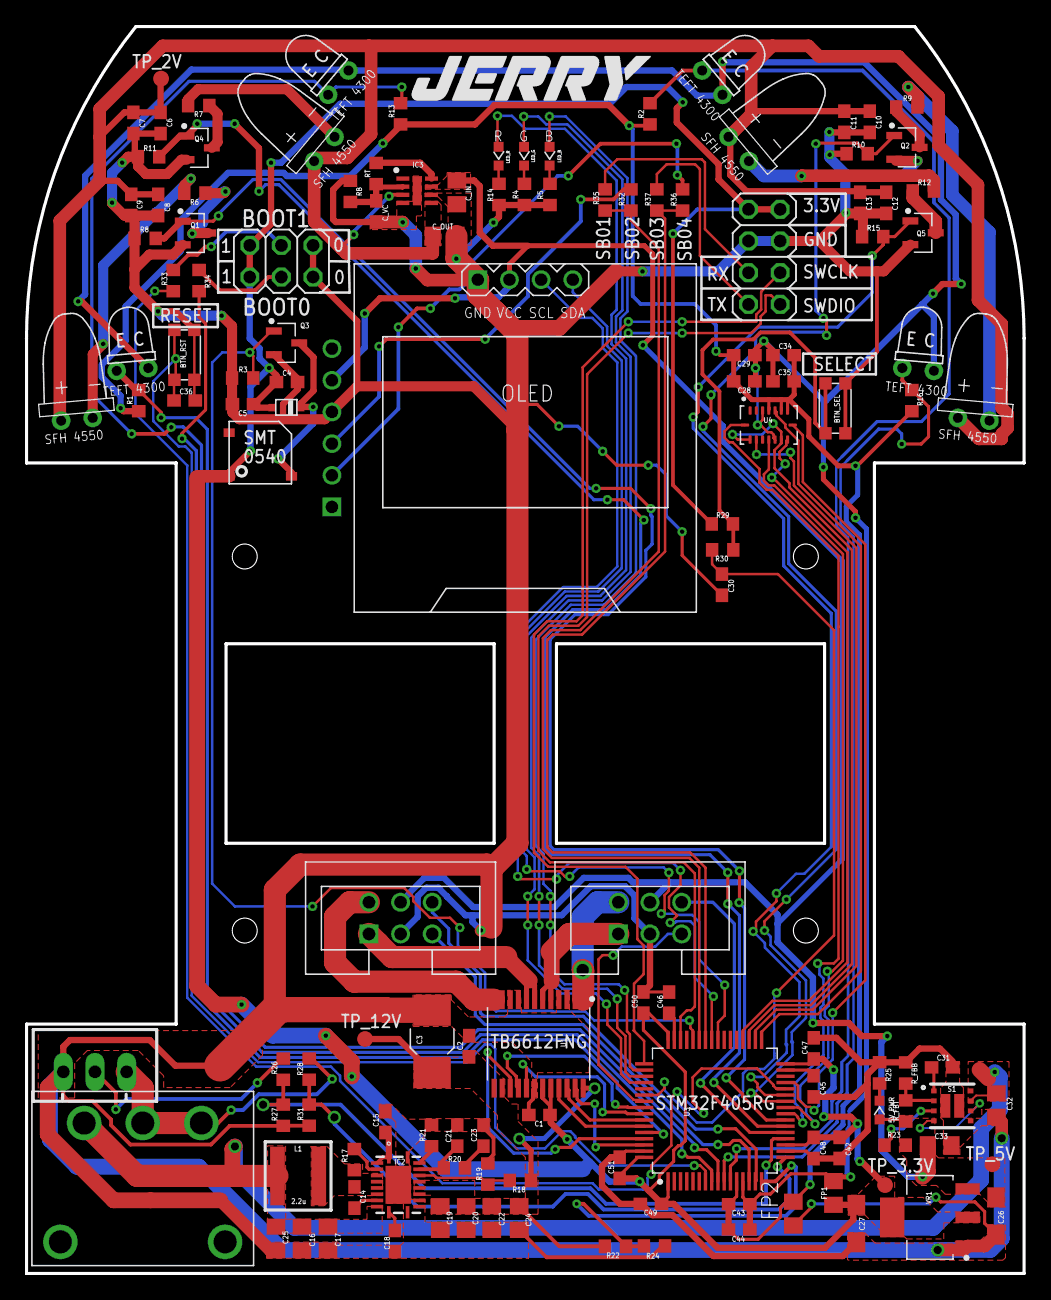
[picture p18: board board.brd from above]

Board: 2 copper layers, 80.0 x 100.0 mm, 135 parts (1 on the bottom side), 94 nets.

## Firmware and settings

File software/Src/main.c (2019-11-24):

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

/* Includes ------------------------------------------------------------------*/
#include "main.h"
#include "adc.h"
#include "dma.h"
#include "i2c.h"
#include "spi.h"
#include "tim.h"
#include "usart.h"
#include "gpio.h"

/* USER CODE BEGIN Includes */
#include <stdio.h>
#include <math.h>
#include <string.h>

//#include "madgwick.h"
//#include "bmi08x.h"
//#include "bmi088.h"

#include "battery.h"
#include "motor.h"
#include "oled.h"
#include "control.h"
#include "ssd1306.h"
#include "bitmaps.h"

/* USER CODE END Includes */


void SystemClock_Config(void);
/* USER CODE BEGIN PFP */

#ifdef __GNUC__
	#define PUTCHAR_PROTOTYPE int __io_putchar(int ch)
#else
	#define PUTCHAR_PROTOTYPE int fputc(int ch, FILE *f)
#endif
PUTCHAR_PROTOTYPE{
	HAL_UART_Transmit(&huart1, (uint8_t *) &ch, 1, 0xFFFF);
	return ch;
}
	
/* USER CODE END PFP */

/* USER CODE BEGIN 0 */

int accNeeded;
int moveSpeed;
int turnSpeed;

void move(int nrCells);

/* USER CODE END 0 */

/**
  * @brief  The application entry point.
  * @retval int
  */
int main(void)
{
  

  /* MCU Configuration--------------------------------------------------------*/

  /* Reset of all peripherals, Initializes the Flash interface and the Systick. */
  HAL_Init();

  /* Configure the system clock */
  SystemClock_Config();

  /* Initialize all configured peripherals */
  MX_GPIO_Init();
  MX_DMA_Init();
  MX_ADC1_Init();
  MX_I2C3_Init();
  MX_SPI2_Init();
  MX_TIM1_Init();
  MX_TIM2_Init();
  MX_TIM3_Init();
  MX_TIM4_Init();
  MX_TIM5_Init();
  MX_USART1_UART_Init();
  MX_TIM14_Init();
  /* USER CODE BEGIN 2 */
	
	// USART UART is causing core to lock up.......
	
	
	oled_init();
	motors_init();
	voltmeter_init();
	
	moveSpeed = speedToCounts(300*2);
	turnSpeed = 30;

	printf("---------- Starting JERRY -----------\r\n");
	
  /* USER CODE END 2 */

  /* Infinite loop */
  /* USER CODE BEGIN WHILE */
  while (1)
  {
    /* USER CODE END WHILE */

    /* USER CODE BEGIN 3 */
		oled_update();
		HAL_Delay(50);
		printf("Running\r\n");
		//curSpeedX = 100;
	  
  }
  /* USER CODE END 3 */
}

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
/* USER CODE BEGIN 4 */
void move(int nrOfCells){

	int totalDistance = nrOfCells * oneCellDistance;
	distanceLeft = totalDistance;
	targetSpeedW = 0; // No curve turns
			
	do{
		accNeeded = needToDecelerate(distanceLeft, curSpeedX, 0);
		if(accNeeded < decX)
			targetSpeedX = moveSpeed;
		else
			targetSpeedX = 0;	
	}while( (encoderCount-oldEncoderCount) < (totalDistance));

	targetSpeedX = 0;	
	oldEncoderCount = encoderCount;
}

/* USER CODE END 4 */
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


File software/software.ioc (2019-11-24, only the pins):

Mcu.UserName=STM32F405RGTx
PA0-WKUP.GPIO_Label=ENC_L_B
PA0-WKUP.Signal=S_TIM5_CH1
PA1.GPIO_Label=ENC_L_A
PA1.Signal=S_TIM5_CH2
PA10.GPIO_Label=RX
PA10.Signal=USART1_RX
PA11.GPIO_Label=BUZZER
PA11.Signal=S_TIM1_CH4
PA13.GPIO_Label=SW_DIO
PA13.Signal=SYS_JTMS-SWDIO
PA14.GPIO_Label=SW_CLK
PA14.Signal=SYS_JTCK-SWCLK
PA15.GPIO_Label=LED_B
PA15.Signal=GPIO_Output
PA2.GPIO_Label=VOLTM_BOOST
PA2.Signal=ADCx_IN2
PA3.GPIO_Label=VOLTM_BATT
PA3.Signal=ADCx_IN3
PA4.GPIO_Label=VOLTM_CELL1
PA4.Signal=ADCx_IN4
PA5.GPIO_Label=ENC_R_A
PA5.Signal=S_TIM2_CH1_ETR
PA6.GPIO_Label=L_EMITTER
PA6.Signal=S_TIM3_CH1
PA7.GPIO_Label=FL_EMITTER
PA7.Signal=S_TIM3_CH2
PA8.GPIO_Label=SCL
PA8.Signal=I2C3_SCL
PA9.GPIO_Label=TX
PA9.Signal=USART1_TX
PB0.GPIO_Label=FR_EMITTER
PB0.Signal=S_TIM3_CH3
PB1.GPIO_Label=R_EMITTER
PB1.Signal=S_TIM3_CH4
PB10.GPIO_Label=SCK
PB10.Signal=SPI2_SCK
PB12.GPIO_Label=CS_GYRO
PB12.Signal=GPIO_Output
PB13.GPIO_Label=CS_ACCEL
PB13.Signal=GPIO_Output
PB14.GPIO_Label=MISO
PB14.Signal=SPI2_MISO
PB15.GPIO_Label=MOSI
PB15.Signal=SPI2_MOSI
PB2.GPIO_Label=BOOT1
PB2.Signal=GPIO_Input
PB3.GPIO_Label=ENC_R_B
PB3.Signal=S_TIM2_CH2
PB4.GPIO_Label=MOTOR_L_IN2
PB4.Signal=GPIO_Output
PB5.GPIO_Label=MOTOR_L_IN1
PB5.Signal=GPIO_Output
PB6.GPIO_Label=MOTOR_R_IN2
PB6.Signal=GPIO_Output
PB7.GPIO_Label=MOTOR_R_IN1
PB7.Signal=GPIO_Output
PB8.GPIO_Label=MOTOR_PWM_L
PB8.Signal=S_TIM4_CH3
PB9.GPIO_Label=MOTOR_PWM_R
PB9.Signal=S_TIM4_CH4
PC0.GPIO_Label=L_RECEIVER
PC0.Signal=ADCx_IN10
PC1.GPIO_Label=FL_RECEIVER
PC1.Signal=ADCx_IN11
PC10.GPIO_Label=LED_G
PC10.Signal=GPIO_Output
PC11.GPIO_Label=LED_R
PC11.Signal=GPIO_Output
PC2.GPIO_Label=FR_RECEIVER
PC2.Signal=ADCx_IN12
PC3.GPIO_Label=R_RECEIVER
PC3.Signal=ADCx_IN13
PC4.GPIO_Label=INT_ACCEL
PC4.Signal=GPIO_Input
PC5.GPIO_Label=INT_GYRO
PC5.Signal=GPIO_Input
PC9.GPIO_Label=SDA
PC9.Signal=I2C3_SDA
PD2.GPIO_Label=BUTTON_SELECT
PD2.Signal=GPXTI2

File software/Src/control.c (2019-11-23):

#include "control.h"
#include "main.h"
#include "motor.h"

// Sensors
float leftSensor = 0;
float rightSensor = 0;
float frontSensor = 0;
float frontSensorTreshhold = 0;
float leftSensorMiddleValue = 0;
float rightSensorMiddleValue = 0;
float sensorError = 0;
float sensorFeedback = 0;;
float sensorScale = 0.1;

//Used for disabling and enabling when the sensors should help guide the mouse and when not to. 
int disableSensorAdjustment = 1;

// Used for control loop
int leftEncoder;
int rightEncoder;
int leftEncoderOld;
int rightEncoderOld;
int leftEncoderChange;
int rightEncoderChange;
int leftEncoderCount;
int rightEncoderCount;
float encoderCount;
float rotationCount;
float oldEncoderCount;
float oldRotationCount;
float encoderChange;
float rotationChange;
float distanceLeft;
float rotationLeft;
int leftBaseSpeed;
int rightBaseSpeed;

float curSpeedX = 0;
float curSpeedW = 0;
int targetSpeedX = 0;
int targetSpeedW = 0;
int encoderFeedbackX = 0;
int encoderFeedbackW = 0;
float rotationalFeedback = 0;
float posErrorX = 0;
float posErrorW = 0;
float oldPosErrorX = 0;
float oldPosErrorW = 0;
int posPwmX = 0;
int posPwmW = 0;
float kpX = 2, kdX = 4;
float kpW = 1, kdW = 10;//used in straight
float accX = 200; // 100 cm/s^2 => 1 m/s^2 
float decX = 200; 
float accW = 2; //cm/s^2
float decW = 2;

int oneCellDistance = distanceToCounts(178);
int quarterTurn = rotToCounts(90);


void speedProfile(void){	
	getEncoderStatus();
	updateCurrentSpeed();
	calculateMotorPwm();      
}


void getEncoderStatus(void)
{
	leftEncoder = - TIM5->CNT;		//read current encoder ticks from register of 32 bit general purpose timer 2
	rightEncoder = - TIM2->CNT;		//read current encoder ticks from register of 32 bit general purpose timer 5

	leftEncoderChange = leftEncoder - leftEncoderOld;
	rightEncoderChange = rightEncoder - rightEncoderOld;
	
	encoderChange = ( rightEncoderChange + leftEncoderChange)/2.0;	 
	rotationChange = (rightEncoderChange - leftEncoderChange)/2.0;

	leftEncoderOld = leftEncoder;
	rightEncoderOld = rightEncoder;
					
	leftEncoderCount += leftEncoderChange;
	rightEncoderCount += rightEncoderChange;
	encoderCount =  (leftEncoderCount+rightEncoderCount)/2.0;	
	rotationCount = (rightEncoderCount - leftEncoderCount)/2.0;
	
	distanceLeft -= encoderChange;
	rotationLeft -= rotationChange;
}



void updateCurrentSpeed(void)
{
	if(curSpeedX < targetSpeedX)
	{
		curSpeedX += (float)(speedToCounts(accX*2)/100);
		if(curSpeedX > targetSpeedX)
			curSpeedX = targetSpeedX;
	}
	else if(curSpeedX > targetSpeedX)
	{
		curSpeedX -= (float)speedToCounts(decX*2)/100;
		if(curSpeedX < targetSpeedX)
			curSpeedX = targetSpeedX;
	}
	if(curSpeedW < targetSpeedW)
	{
		curSpeedW += accW;
		if(curSpeedW > targetSpeedW)
			curSpeedW = targetSpeedW;
	}
	else if(curSpeedW > targetSpeedW)
	{
		curSpeedW -= decW;
		if(curSpeedW < targetSpeedW)
			curSpeedW = targetSpeedW;
	}	
}


void calculateMotorPwm(void) // Position and rotation PD controller
{	
	
	// PD loop for translation and rotation to generate base speed for both motors
	encoderFeedbackX = rightEncoderChange + leftEncoderChange;
	encoderFeedbackW = rightEncoderChange - leftEncoderChange;	
	 
	// Have sensor error properly scale to fit the system
	//sensorFeedback = sensorError / sensorScale; 
	
	if(disableSensorAdjustment)
		sensorFeedback = 0;
	
	rotationalFeedback = encoderFeedbackW + sensorFeedback;

	posErrorX = curSpeedX - encoderFeedbackX;
	posErrorW = curSpeedW - rotationalFeedback;
	
	posPwmX = kpX * posErrorX + kdX * (posErrorX - oldPosErrorX);
	posPwmW = kpW * posErrorW + kdW * (posErrorW - oldPosErrorW);
	
	oldPosErrorX = posErrorX;
	oldPosErrorW = posErrorW;
	
	leftBaseSpeed = posPwmX - posPwmW;
	rightBaseSpeed = posPwmX + posPwmW;

	SET_PWM_L(leftBaseSpeed);
	SET_PWM_R(rightBaseSpeed);
}

int needToDecelerate(int32_t dist, int16_t curSpd, int16_t endSpd)//speed are in encoder counts/ms, dist is in encoder counts 
{
	if (curSpd<0) curSpd = -curSpd;
	if (endSpd<0) endSpd = -endSpd;
	if (dist<0) dist = -dist;			//-dist;
	if (dist == 0) dist = 1;  //prevent divide by 0

	int a = countsToSpeed((curSpd*curSpd - endSpd*endSpd)*100/dist/4/2);
	
	if(a < 0)
		a = -a;
	
	
	return a;
	
	
	//calculate deceleration rate needed with input distance, input current speed and input targetspeed to determind if the deceleration is needed
	//use equation 2*a*S = Vt^2 - V0^2  ==>  a = (Vt^2-V0^2)/2/S
	//because the speed is the sum of left and right wheels(which means it's doubled), that's why there is a "/4" in equation since the square of 2 is 4
}

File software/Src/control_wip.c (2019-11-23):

#include "control_wip.h"
#include "main.h"


#define WHEEL_TO_WHEEL 80 // Center of wheel to the center of the other wheel. (mm) 
#define WHEEL_D 21 				// Wheel diameter (mm)
#define CPR 2048.0				// Counts per revolution
#define PI 3.141592			
#define GEARING (60.0/16.0)

typedef struct{
	int counts;
	int counts_old;
	int counts_total;
	int counts_change;
}encoder_t;

typedef struct{
	encoder_t left;
	encoder_t right;
	float counts;
	float counts_old;
	float counts_change;
	float rotations;
	float rotation_change;
	float rotation_old;	
}encoders_t;

typedef struct {
	encoders_t encoders;
	float distance_left;
	float rotation_left;
	float current_speed_x;
	float target_speed_x;
	float current_speed_w;
	float target_speed_w;
	float acc_x;
	float acc_w;
	float dec_x;
	float dec_w;
	int left_base_speed;
	int right_base_speed;
}controller_t;

encoder_t encoder_left;
encoder_t encoder_right;
encoders_t encoders;
controller_t controller;


// Functions
void contro_loop(void){	
	update_encoder();
	update_sensor_error();
	update_current_speed();
	update_motor_pwm();      
}

void controller_init(void){
	encoders.left = encoder_left;
	encoders.right = encoder_right;
	controller.encoders = encoders;
}

void update_encoder(void){
	
	encoder_left.counts = TIM2->CNT;	//read current encoder ticks from register of 32 bit general purpose timer 2
	encoder_right.counts = TIM5->CNT; //read current encoder ticks from register of 32 bit general purpose timer 5

	encoder_left.counts_change = encoder_left.counts - encoder_left.counts_old;
	encoder_right.counts_change = encoder_right.counts - encoder_right.counts_old;
	
	encoders.counts_change = (encoder_right.counts_change + encoder_left.counts_change) / 2.0f;
	encoders.rotation_change = (encoder_right.counts_change - encoder_left.counts_change) / 2.0f;

	encoder_left.counts_old = encoder_left.counts;
	encoder_right.counts_old = encoder_right.counts;

	encoder_left.counts_total += encoder_left.counts_change;
	encoder_right.counts_total += encoder_right.counts_change;
	
	encoders.counts = (encoder_left.counts + encoder_right.counts) / 2.0f;
	encoders.rotations = (encoder_right.counts - encoder_left.counts) / 2.0f;
	
	controller.distance_left -= encoders.counts_change;
	controller.rotation_left -= encoders.rotation_change;
}



void update_current_speed(void)
{
	if(controller.current_speed_x < controller.target_speed_x)
	{
		controller.current_speed_x += (float)(speed_to_counts(controller.acc_x*2) / 100);
		if(controller.current_speed_x > controller.target_speed_x)
			controller.current_speed_x = controller.target_speed_x;
	}
	else if(controller.current_speed_x > controller.target_speed_x)
	{
		controller.current_speed_x -= (float)speed_to_counts(controller.dec_x*2)/100;
		if(controller.current_speed_x < controller.target_speed_x)
			controller.current_speed_x = controller.target_speed_x;
	}
	if(controller.current_speed_w < controller.target_speed_w)
	{
		controller.current_speed_w += controller.acc_w;
		if(controller.current_speed_w > controller.target_speed_w)
			controller.current_speed_w = controller.target_speed_w;
	}
	else if(controller.current_speed_w > controller.target_speed_w)
	{
		controller.current_speed_w -= controller.dec_w;
		if(controller.current_speed_w < controller.target_speed_w)
			controller.current_speed_w = controller.target_speed_w;
	}	
}


void update_motor_pwm(void){	
	
	// PD loop for translation and rotation to generate base speed for both motors
	encoderFeedbackX = rightEncoderChange + leftEncoderChange;
	encoderFeedbackW = rightEncoderChange - leftEncoderChange;	
	 
	//Have sensor error properly scale to fit the system
	sensorFeedback = sensorError / sensorScale; 
	
	if(disableSensorAdjustment)
		sensorFeedback = 0;
	
	rotationalFeedback = encoderFeedbackW + sensorFeedback;

	posErrorX += curSpeedX - encoderFeedbackX;
	posErrorW += curSpeedW - rotationalFeedback;
	
	posPwmX = kpX * posErrorX + kdX * (posErrorX - oldPosErrorX);
	posPwmW = kpW * posErrorW + kdW * (posErrorW - oldPosErrorW);
	
	oldPosErrorX = posErrorX;
	oldPosErrorW = posErrorW;
	
	leftBaseSpeed = posPwmX - posPwmW;
	rightBaseSpeed = posPwmX + posPwmW;

	setLeftPWM(leftBaseSpeed);
	setRightPWM(rightBaseSpeed);	
}

void getSensorError(void){
	leftSensor = calcDistances[0];
	frontSensor = calcDistances[1];
	rightSensor = calcDistances[2];
	
	/*
	// Stop the mouse from running when the mouse runts into walls, not tested.
	if((leftSensor < leftSensorMiddleValue || rightSensor < rightSensorMiddleValue) 
		&& frontSensor < frontSensorTreshhold){
			enableControlLoop = 0;
			setLeftPWM(0);
			setRightPWM(0);
		}
	*/
		
	
	if(leftSensor < leftSensorMiddleValue && rightSensor > rightSensorMiddleValue /*&& rightSensor < 10*/)
		if(rightSensor > 8)
			sensorError = leftSensorMiddleValue - leftSensor - 0.5;
		else
			sensorError = leftSensorMiddleValue - leftSensor;
	else if(rightSensor < rightSensorMiddleValue && leftSensor > leftSensorMiddleValue /*&& leftSensor < 10*/)
		if(leftSensor > 8)
			sensorError = rightSensor - rightSensorMiddleValue;
		else
			sensorError = rightSensor - rightSensorMiddleValue - 0.5;
	else
		sensorError = 0;
}

int need_to_decelerate(int32_t dist, int16_t curSpd, int16_t endSpd)//speed are in encoder counts/ms, dist is in encoder counts 
{
	if (curSpd<0) curSpd = -curSpd;
	if (endSpd<0) endSpd = -endSpd;
	if (dist<0) dist = -dist;			//-dist;
	if (dist == 0) dist = 1;  //prevent divide by 0

	int a = counts_to_speed((curSpd*curSpd - endSpd*endSpd)*100/dist/4/2);
	
	if(a < 0)
		a = -a;
	
	
	return a;
	
	
	//calculate deceleration rate needed with input distance, input current speed and input targetspeed to determind if the deceleration is needed
	//use equation 2*a*S = Vt^2 - V0^2  ==>  a = (Vt^2-V0^2)/2/S
	//because the speed is the sum of left and right wheels(which means it's doubled), that's why there is a "/4" in equation since the square of 2 is 4
}

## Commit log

2019-06-06 Initial Upload
    Just some basic components added with symbols, footprints and 3D packages.
    [board.sch]
2019-07-07 Update Motor driver -> MAX14870
    [board.sch]
2019-08-01 2V regulator + new motor driver
    Changed motor driver from MAX14870 to TB6612FNG for easier soldering. Added a 2V switching DC regulator for more efficient emitter driving.
    [board.sch]
2019-08-07 Power Regulators + Created board file
    Alot has been done in this update.
    [board.brd, board.sch]
2019-08-12 Voltmeter Monitors on Boost, Batt, Cell1 and 5V Power LED
    [board.brd, board.sch]
2019-08-12 Visual update for ground splitter
    [board.brd, board.sch]
2019-08-24 Changed IMU to bosch BMI088
    [board.brd, board.sch]
2019-08-26 Pin Setup on MCU
    [board.brd, board.sch]
2019-08-26 VSS + VDD
    [board.brd, board.sch]
2019-08-29 Oled + Hc05
    [board.brd, board.sch]
2019-08-29 Regulator board placement
    [board.sch]
2019-08-29 switch layout on board
    [board.brd, board.sch]
2019-08-31 Eagle 9.5 persistent group update
    [board.brd, board.sch]
2019-09-01 3D Packages update
    [C0603.step, HC-05.step, IDC-6.step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]
2019-09-01 More 3D Models
    [C0402.step, C0805.step, C1206.step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]
2019-09-02 3D packages and footprint updates + board picture
    [500SSP1S1M6QEA-Switch.step, BMI088.step, HALX5030-222.step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]
2019-09-03 3D packages + component layout
    [board.brd, board.sch, motor_mount.dxf]
2019-09-05 Routing power
    [board.brd, board.sch]
2019-09-06 Routing top side
    [board.brd]
2019-09-07 Folder structure update and routing on PCB
    [500SSP1S1M6QEA-Switch.step, BMI088.step, C0402.step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]
2019-09-09 silcscreen changes
    [board.brd]
2019-09-10 TPS61088 update
    [board.sch]
2019-09-24 BOM update
    [BOM_board.csv, board.brd]
2019-10-04 Removed backup files
    Eagle generated backup files, removed those
    [BOM_board.csv, board.brd, board.sch]
2019-10-13 Keil Setup
    [BOM_board.csv]
2019-10-13 Bug fix on project setup
    [main.c, main.h, software.ioc]
2019-10-14 Battery ADC DMA printout
2019-10-14 Motor Test
2019-10-14 Button interrupt
2019-10-15 Battery Voltage Sampling
2019-10-17 Battery & Motor API
2019-10-17 oled error print function
    [main.c, oled.c]
2019-10-17 frequency change on motor PWM + error printing
    [battery.c, main.c, motor.c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]
2019-10-17 button select menu
2019-11-23 bitmap drawer (almost working)
    [board.brd, board.sch]

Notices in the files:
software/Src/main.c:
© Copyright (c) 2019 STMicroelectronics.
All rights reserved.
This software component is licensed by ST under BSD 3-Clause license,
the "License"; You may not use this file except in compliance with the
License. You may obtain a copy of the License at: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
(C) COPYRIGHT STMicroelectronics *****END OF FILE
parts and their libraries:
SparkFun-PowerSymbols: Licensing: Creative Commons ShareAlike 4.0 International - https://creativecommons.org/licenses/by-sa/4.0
